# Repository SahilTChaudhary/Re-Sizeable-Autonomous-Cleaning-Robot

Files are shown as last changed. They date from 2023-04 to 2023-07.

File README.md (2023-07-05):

# ABSTRACT

Cleaning robots have advanced significantly in recent years, owing to their increased market presence and the desire for improved performance in cleaning. However, owing to their geometric restrictions with respect to the cleaning area, most robots have difficulty in cleaning the entire area. The robot developed in this paper uses on-board sensors, including ultrasonic sensors and camera to detect obstacles, change the robot configuration accordingly, and navigate forward, backward and even sideways with the help of Mecanum wheels. A ball screw linear actuator has been used to change the length of the robot according to what it maps about the room using the sensors. To achieve this, a precise CAD model has been developed according to the decided parameters. A functional prototype has also been developed as a proof of concept and it has been compared with a simulation study done in CoppeliaSim software.

---

**Work Done**

* Designed a CAD model using Fusion 360
* Calculated the Wheel Motor Torque requirements and the Battery Life
* Conducted a Simulation study in CoppeliaSim (V-REP)
* Programmed the Robot and Sensors using Raspberry Pi 4
* Conducted a Static Stress Analysis on the chassis of the robot using Ansys
* Built a Functional Prototype

<div style="text-align:center">
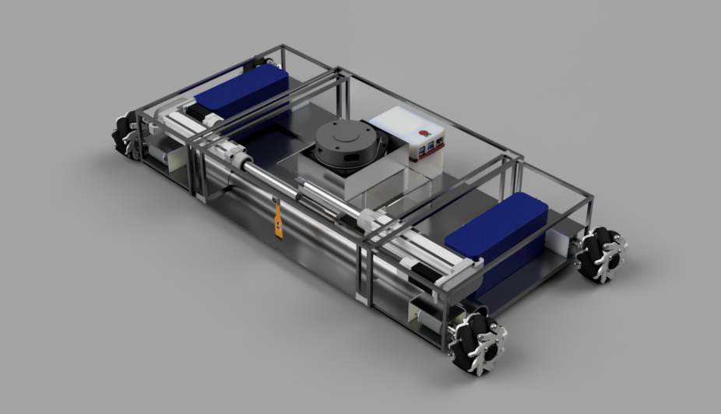
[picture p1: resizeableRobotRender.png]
cleaning_robot

</div>
<div style="text-align:center">
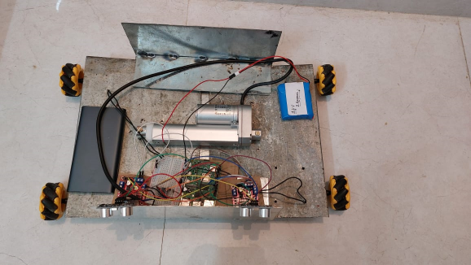
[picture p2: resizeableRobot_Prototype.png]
cleaning_robot

</div>

---

# CONCLUSION

A simulation study has been demonstrated to verify the efficacy of the system. Further, a functional prototype has been developed as a proof of concept to test the system in the real world. A static stress analysis has been conducted to determine the factor of safety of the chassis, which is the main load bearing element of the robot. Since the chassis is made of MS sheet, the weight of components will introduce stresses and bending. The stress analysis as well as the model developed prove that bending and subsequent failure are not a problem. Future work will involve integrating SLAM using LIDAR, for more efficient and systematic cleaning.
The analysis results show that the Factor of Safety is 15, hence the chassis will not fail. The maximum displacement is 0.3745 mm, which is at the middle box chassis. Further, the maximum stress induced is 14.75 MPa.
A Simulation environment has extremely ideal conditions, and there are no stresses induced on the robot. However, in the real world, there are several factors such as weight of components and friction that affect the performance of the robot. As a result, several iterations were required to attain a chassis that was performing well. Earlier iterations of the functional prototype suffered from bending of the chassis and loss of traction to the wheels. Having identified the problem areas, necessary modifications were made to the chassis to ensure compliance. After several iterations, a chassis was finally developed that functioned well. Such complications are not faced in a Simulation study, hence developing a functional prototype is of utmost importance, and has its own set of challenges.

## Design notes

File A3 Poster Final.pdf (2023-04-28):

References

Re-Sizeable Autonomous Cleaning Robot

Conclusion and Discussion

Introduction | Result and Discussion
- There is a strong demand for the application of cleaning robots in domestic settings. • Most robots in the market are of a fixed configuration. • Development of a re-sizeable robot that can increase its size in open spaces to cover more area in a single sweep, or can reduce its size to reach inaccessible areas is the focus of this project.

Scope of the Project

Presenter Details

- The project focuses on the development of a re-sizeable cleaning robot. The re-sizing mechanism can also be exported to other robots depending on needs.
- Definition of the problem statement and development of the Functional Architecture.
- Finalization of components and development of CAD model.
- Conduction of a Simulation study and development of a Functional Prototype as a proof of concept.

Methodology

- A simulation study has been conducted to demonstrate the efficacy of the system.
- A Functional Prototype has been developed to compare with the Simulation study.
- A stress analysis on the MS sheet used to make the chassis has been conducted. The FOS is 15.

A simulation study has been demonstrated to verify the efficacy of the system. Further, a functional prototype has been developed as a proof of concept to test the system in the real world. A static stress analysis has been conducted to
determine the factor of safety of the chassis, which is the main load bearing element of the robot. Since the chassis is made of MS sheet, the weight of components will introduce stresses and bending. The stress analysis as well as the model developed prove that bending and subsequent failure are not a problem. Future work will involve integrating SLAM using LIDAR, for more efficient and systematic cleaning.

Minimum Length

Maximum Length

- Designing and Optimization of An Autonomous Vacuum Floor Cleaning Robot
- Autonomous Self-Reconfigurable Floor Cleaning Robot
- Development of a Vacuum Cleaner Robot

SAHIL T CHAUDHARY – 18BME0668 KAHAAN PATEL – 18BME0691
MEHUL CHAURASIA – 18BME0640

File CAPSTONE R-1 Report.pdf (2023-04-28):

# Re-Sizeable Autonomous Cleaning Robot

### Submitted in partial fulfilment of the requirements for the degree of

# Bachelor of Technology

in

# Mechanical Engineering

By

### Sahil Chaudhary (18BME0668)

### Kahaan Patel (18BME0691)

### Mehul Chaurasia (18BME0640)

### Under the guidance of

### Prof. / Dr. Chinmaya Sahu

### Department of Design and Automation

School of Mechanical Engineering, VIT, Vellore.

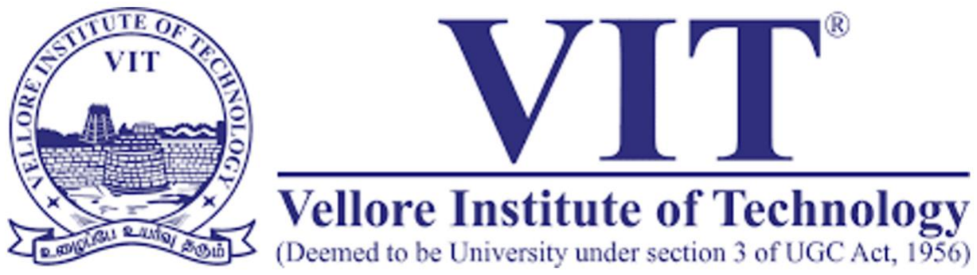
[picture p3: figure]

### February 2022

# Declaration

### We hereby declare that the thesis entitled “Re-Sizeable Autonomous Cleaning

### Robot" submitted by Kahaan Patel (18BME0691), Sahil Chaudhary

### (18BME0668) and Mehul Chaurasia (18BME0640), for the award of the degree

### of Bachelor of Technology in Mechanical Engineering to VIT is a record of

bonafide work carried out by me under the supervision of Dr. Chinmaya Sahu.

### We further declare that the work reported in this thesis has not been submitted

### and will not be submitted, either in part or in full, for the award of any other

degree or diploma in this institute or any other institute or university.

### Place: Vellore

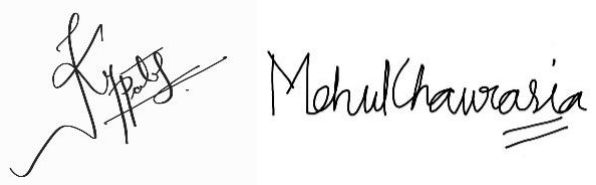
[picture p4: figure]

Date: 12th February 2022 | Signature of the Candidates

# Certificate

### This is to certify that the thesis entitled “Re-Sizeable Autonomous Cleaning

### Robot” submitted by Kahaan Patel (18BME0691), Sahil Chaudhary

### (18BME0668) and Mehul Chaurasia (18BME0640), School of Mechanical

### Engineering, VIT University, for the award of the degree of Bachelor of

### Technology in Mechanical Engineering, is a record of bonafide work carried out

### by them under my supervision during the period, 15.01.2022 to 20.04.2022, as

per the VIT code of academic and research ethics.

### The contents of this report have not been submitted and will not be submitted

### either in part or in full, for the award of any other degree or diploma in this

### institute or any other institute or university. The thesis fulfils the requirements

### and regulations of the University and in my opinion meets the necessary standards

for submission.

### Place: Vellore

Date: 12th February 2022 | Signature of the Guide
Internal Examiner | External Examiner

### Head of the Department

### School of Mechanical Engineering

# List of Contents

Contents | Page No.
Declaration | i
Certificate | ii
List of Contents | iii
Acknowledgement | iv
Abstract | 1
Introduction | 1
Literature Review | 2
Gaps in the Literature | 5
Problem Definition | 5
Objectives | 5
Methodology | 5
Worked Carried Out So Far | 5
Design Prototype | 6
Work to be Done | 8
Gantt Chart | 8
Milestones in the Project Phase | 8
References | 9

# Acknowledgement

We, Kahaan Patel, Sahil Chaudhary and Mehul Chaurasia would like to thank Dr. Chinmaya Sahu for his valuable guidance throughout the course of this project.

### We would also like to give a special thanks to Mukul Ganwal for his support

throughout the project.

### Abstract:

Cleaning robots have advanced significantly in recent years, owing to increased market presence and the demand for improved cleaning performance. However, due to geometric restrictions of the platforms in relation to the cleaning stage, as well as furniture and architecture, most robots have difficulty covering the whole cleaning area. The aim is to use the on-board sensors which will mainly be a combination of SLAM (Simultaneous Localization and Mapping) integrated using LIDAR and camera to detect obstacles and change the robot configuration accordingly and to navigate forward and backward and even sideways with the help of Mecanum wheels. The plan is to use a ball screw actuation mechanism to change the length of the robot according to what it maps about the local terrain using the sensors. For this purpose, a precise CAD model will be designed with the decided parameters so as to bring down the cost of making the cleaning robot to the bare minimum while also optimizing its cleaning efficiency at the same time.

### Introduction:

Cleaning has always been an important and necessary aspect of human lives, and it has developed and changed over time. The need for completely automated floor cleaning robots has surged as a result of today's hectic lifestyle.

Automated floor cleaning robots are commonly employed in smart homes, residential, and office spaces to clean the floors.

According to a world market study, there is a strong demand for the application of these robots in domestic settings with fully automated functionalities and the least amount of human assistance, and while these robots still account for a small percentage of the global vacuum cleaner market, their recognition and implementation is growing at a rapid rate.

The robots are small and execute the cleaning operation without the need for human participation. These robots use motion planning algorithms to cover a large area while cleaning, such as spiral motion, backtracking spiral motion, boustrophedon motion (back and forth), and basic zig-zag motion patterns.

Even though fixed-configuration robots have sufficient path planning and motion skills, they may require more time and energy to complete the complicated task effectively than their changeable counterparts. As a result, building a re-sizeable robot that can increase the swept area in open spaces, and can reduce its size to reach inaccessible areas. This project focuses on the design and development of the same.

### Literature Review:

Prassler et al. demonstrated almost how all commercial home cleaning robots are equipped with vacuum cleaners as their primary means of cleaning. Pool cleaning robots have also been developed. Some robots also have wet scrubbers to clean the floor (non-textile floor coverings), and some also clean carpets. Some industrial robots have sweepers along with vacuum cleaners. Duct cleaning robots with rotating brushes have also been developed. Sensors that are usually employed include Ultrasonic, LIDAR, IR, Cameras and Contact. Robots are navigated using dead-reckoning, manually using a joystick, or even using magnetic markers to guide the way. Safety features include front bumpers that absorb impact shock. Robot road sweepers have also been developed for cleaning large open spaces. [1]

Endres et al. developed robots for cleaning purposes in the supermarkets. There are some special features in these robots, they consist of a retractable wing which is inserted in the right part of the robot. The use of this retractable wing allows the robot to get close to the objects and precisely cleans the floor without colliding with the obstacles. Also, the size of this wing can be adjusted according to the requirement it can be extended or reduced as needed. The main features of this robot were: To identify the obstacles properly for cleaning the environment, executing the plan properly, no need to install any additional part to localize the robot, a systematic skill to move around the obstacles for least energy consumption. [2]

Kushal et al. have worked on a cleaning robot ATMEGA 2560 which worked with two modes: automatic and manual. The hardware used were Arduino Mega 2560, Ultrasonic Sensor, DC Generated Motor, Vacuum Motor, L298n Dual H-Bridge Motor Driver, VL53LOX Laser TOF Sensor and Servo Motor. Since the robot has two modes, one of them is manual mode which is selected when the robot switch is high and allows the users to reach places which are not automatically detected by the robot. And for the autonomous mode there is an algorithm which is followed by the robot with path planning. There is also a water sprayer attached so that the robot can also be used for the moping purposes as for the convenience of the user. [3]

Sewan Kim et al. demonstrated the Roboking system integration in an autonomous cleaning robot. The purpose of this robot was the protection of the indoor cleaning environment while the robot is working. There are many different sensors and the functions which are integrated in this system. The robot uses a digital signal processor from Texas Instruments (320LF 2406A). It works on 40MHz frequency with 24 sensors performing the operations together gathering different signals from internal subsystems. Also, there are 14 ultrasonic sensors which are installed in the robot, where nine of them were used in the lower part to find the obstacles. And the others were used on the upper part so that the robot does not collide with the tall obstacles. For the Roboking mechanism, there are cliff detecting sensors which determine the upliftment of the robot and prevent the robot from falling down. [4]

Liu et al. developed a system that did not rely on mapping and global self-localization. It consists of three layers. The lowest layer contains the sensors and hardware, which include ultrasonic (13 pairs, 7 for the front and the rest for the sides), IR, encoders, DC motors, vacuum etc. The second layer is responsible for the behaviour of the robot, which include point turning, line following, wall following, side shifting, and obstacle rounding. The third layer is responsible for carrying out tasks, like environment learning, cleaning and homing. [5]

Mahmud Hasan et al. demonstrated the use of bumper contact sensors and cliff IR sensors. The path planning algorithms include Random walk, spiral, ‘S’-shaped path and wall follow. These four algorithms are cycled between until the entire area is covered. The motor specification is 2Amp/6VDC, 5500 rpm with 70:1 gearbox for the driving wheels. The side brush controlling motor specification is 0.5Amp/6VDC with a 30:1 gearbox. The vacuum motor is 5Amp/6VDC with 8000rpm (Cyclonic type dry vacuum is used). The battery used is 6V/4.5Ah lead-acid. The robot can operate for an hour. The battery takes 5-6 hours to charge. [6]

Joon et al. developed a combination of Lidar and camera. A manipulator arm containing the vacuum was attached to the mobile robot. The collector box has a volume of 378 cubic cm (10 cm × 6 cm × 6.3 cm). [7]

Shakhawat Hossen et al. discussed how LIDAR and GPS have been used for mapping and localization. IR proximity sensors and ultrasonic sensors were used for object detection. [8]

Gerstmayr-Hillen et al. discussed how an omnidirectional camera was used to generate panoramic images of the environment in order to map it, and hence guide and navigate the robot to cover a rectangular segment of the robot’s workspace. The omnidirectional camera is used to simultaneously localize the robot and also map the environment. Hence, the camera carries out local visual homing and provides the data to generate a dense topological map. The robot is guided along parallel paths by controlling its distance from the previous lane. The distance is estimated using images from the camera and the robot’s odometry. Only the robot’s distance from the previous lane and its orientation are calculated. [9]

Karur et al. discussed various path planning algorithms. Dijkstra and A* algorithms are used for static environments, whereas D*RRT (Rapidly-Exploring Random Trees), Genetic, Ant Colony and Firefly algorithms are used for Dynamic environments. [10]

Dakulovic et al. demonstrated complete coverage of D* algorithm for path planning, using a combination of D* and PT algorithms. [11]

Lamini et al. demonstrated how GA (Genetic Algorithm) with improved crossover operators and fitness functions were employed to find optimal solutions. [12]

Amine Yakoubi et al. demonstrated that GA was used for path planning. Each gene represents the robot position and the chromosomes represent the mini-path. [13]

Liu et al. developed an algorithm for complete coverage path planning, which combines random path planning and local complete coverage path planning. Random path planning is very flexible for unstructured environments, but is inefficient. On the other hand, local complete coverage path planning generates a comb-like path to cover a relatively small area with high efficiency, but fails to do so in a larger area in an unstructured and dynamic environment. The proposed technique combined the benefits of both. 11 pairs of ultrasonic sensors were used, 7 for the front and the rest for the sides. [14]

Hofner et al. demonstrated path planning of a rectangular non-holonomic robot. Two changing maneuvers were used to navigate the robot – U-Turn and Side-Shift. Based on the parameters of the robot and the environment, the path planning algorithm will choose the most appropriate path planning template such that the entire floor area is covered efficiently. Localization was done using ultrasonic sensors and dead-reckoning. Subgoals were determined in the vicinity of various pre-planned landmarks. Vehicle guidance was done by finding the specified start location and compensation of path errors. [15]

Ramalingam et al. developed an algorithm for detecting and classifying debris as solid and liquid spillage using CNN and SVM was developed. This helped the robot to avoid hard to clean debris, as robots are mostly unable to clean such debris and hence end up spreading them on the floor rather than cleaning it, thus also reducing their efficiency. [16]

Schmidt et al. developed an algorithm that has been developed to memorize uncleaned areas that couldn’t be cleaned in the first sweep because of a temporary obstacle, and then come back to clean it after the remaining area has been cleaned. [17]

Parween et al. developed a self-reconfigurable robot called hTrihex has. It enables the robot to cover spaces that are generally missed or inaccessible by the usual circular shaped cleaning robots (like corners). This robot can configure itself into three different configurations based on the requirements, namely – Straight, Chevron and Closed. The sensors used onboard are encoders, LIDAR and IMU, along with a PID controller for implementing a closed-loop system. A differential drive has been implemented to steer the robot and hence control the heading. [18]

Parween et al. developed another similar self-reconfigurable robot is the hTetrakis. It consists of four equilateral triangles, and can change between three configurations namely – “I”, “A”, and “U” shapes. These configurations enable the robot to access convex and narrow corners that are generally inaccessible by the common circular shaped cleaning robots. [19]

Forlizzi et al. demonstrated that mecanum wheels have their omnidirectional property that allow them to have excellent manoeuvrability and ability to move in a congested space. Congested spaces usually mean environments with static or dynamic obstacles or narrow areas respectively. Due to the Mecanum wheel’s high manoeuvrability, it is ideal for outdoor applications like transportation purposes in warehouses, mining activities and even for military activities and indoor applications like autonomous robot cleaning that is the objective of this Capstone project. [20]

Laurena et al. developed and demonstrated control mechanism for actuating ball screw linear actuator. A ball screw linear actuator converts rotatory motion to linear motion. It has low friction and can withstand thrust loads. The programming and control system for the linear actuator was developed. [21]

Bhowmik et al. developed an algorithm for navigation of a cleaning robot by modifying the Dijkstra algorithm. A provision for backtracking and hill climbing were incorporated. This improved the performance of the Dijkstra algorithm. [22]

### Gaps in the Literature:

After the exhaustive literature review it has been concluded that,

1. All the commercially available cleaning robots are fixed in size and configuration.
2. A handful of self-reconfigurable robots have been developed. The aim of these robots is to cover hard-to-reach places, that conventional fixed configuration robots cannot.
3. Hence, the aim is to develop a re-sizeable robot that can increase its length to cover more area in a single sweep, and can also reduce its size to reach inaccessible areas.

### Problem Definition:

Cleaning robots are available in a variety of sizes and can clean a specific area in a single sweep. However, in open places with little impediment, such as broad halls and living rooms, cleaning can be done quickly by sweeping a larger area in a single sweep. To address this issue, a re- sizeable cleaning robot is being developed that can extend its length, allowing it to cover a larger area in a single sweep, and can also reduce its size to reach inaccessible areas.

### Objectives:

1. To design a system that can change the length of the robot depending on the need and area that is currently being cleaned.
2. To integrate an actuation mechanism for changing the length.
3. To integrate SLAM using LIDAR.
4. To integrate object detection using camera and/or ultrasonic sensors.

### Methodology:

The theoretical design of the robot, as well as the basic components needed, have been finalised after extensive study and detecting gaps in the literature review, as well as recognising scope for improvement. The following steps will be to create a CAD model, programme the robot's many functions like the ability to change its length according to the environment, and do simulations like controlling the opening and closing of the vacuum suction hole and the ability of the robot to manoeuvre with the help of Mecanum wheels. The on-board sensors will include LIDAR and camera to detect obstacles and change the robot configuration accordingly.

### Work Carried Out So Far:

1. Literature review has been completed.
2. Problem statement defined.
3. The primary components required to make the robot have been finalised.
4. The conceptual design of the robot, including the mechanism to change its size, has been developed.

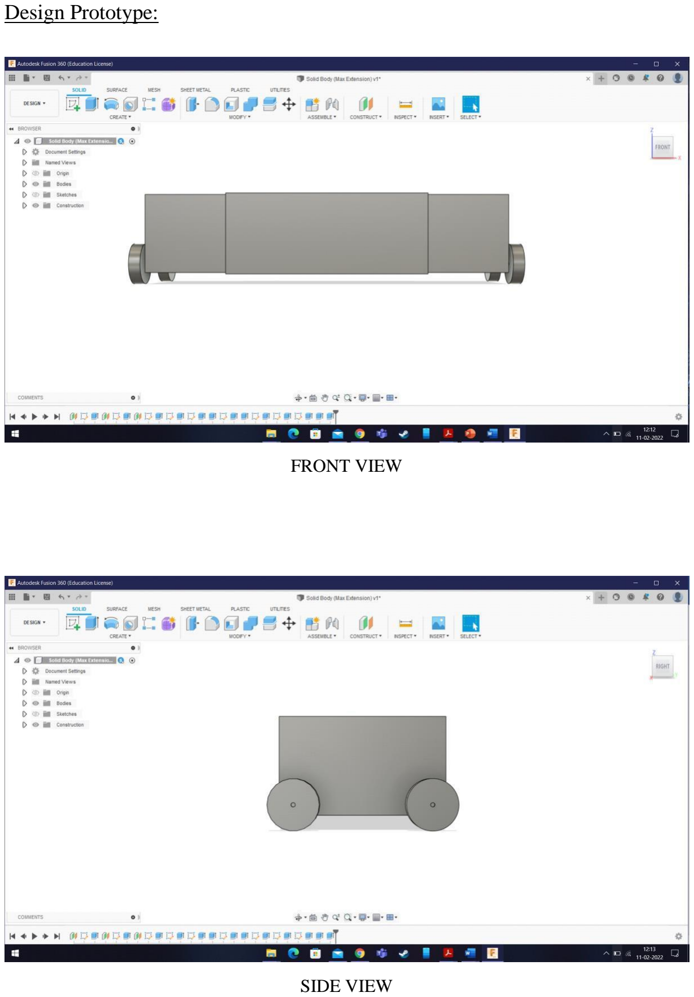
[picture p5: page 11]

### Design Prototype:

FRONT VIEW

SIDE VIEW

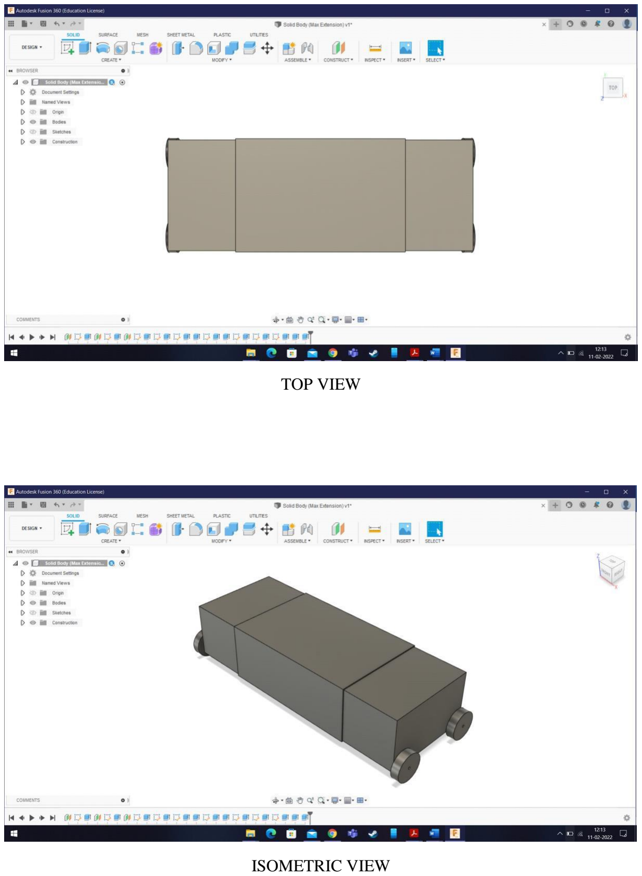
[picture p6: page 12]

TOP VIEW

ISOMETRIC VIEW

### Work to be Done:

1. A CAD model for the robot- After deciding upon the dimensions, the objective is to model it in Autodesk Fusion 360 so as to achieve the goal of making a re-sizeable autonomous robot that can change its dimensions according to the terrain.
2. Integrating SLAM using LIDAR and object detection using camera- Simultaneous Localization and Mapping will be used by the cleaning robot to create a map of the terrain and the concept of Light Detection and Ranging is used which collects information about variable distances between the robot and an obstruction using light in the form of a pulsed laser.
3. Developing the control system to actuate the Ball Screw Linear Actuator used to change the size (length) of the robot.
4. Integrating Mecanum wheels control in the robot.
5. Designing size changing vacuum slit for the robot- The size of the vacuum opening needs to change proportionally along with the length of the robot.
6. Integrating Dijkstra algorithm for path planning.

### Gantt Chart:

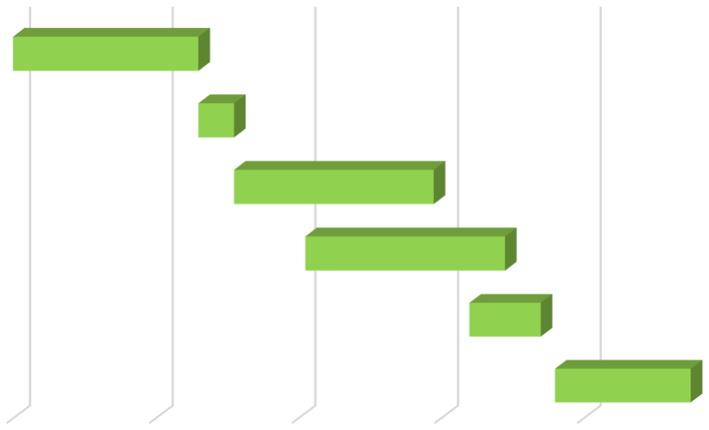
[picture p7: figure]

### Milestones in the Project Phase:

1. Chassis design
2. CAD design for actuation mechanism
15-Jan | 04-Feb | 24-Feb | 16-Mar | 05-Apr

Literature Review

Design Planning

Computer Aided Design

Coding

Integrating Everything

Simulation

| Everything Simulation | | Aided Design Coding Integrating Computer | Design Planning | Literature Review
Start Date | 01-Apr | 20-Mar | 25-Feb | 15-Feb | 10-Feb | 15-Jan
Days to Complete | 20 | 10 | 28 | 28 | 5 | 26

### Gantt Chart

3. Path Planning Algorithm
4. Object Detection Algorithm
5. Developing the control system to actuate the Ball Screw Linear Actuator used to change the size of the robot

### References:

[1] E. Prassler, A. Ritter, C. Schaeffer and P. Fiorini, “A Short History of Cleaning Robots,” Autonomous Robots, vol. 9, pp. 211-226, December 2000.
[2] H. Endres, W. Feiten and G. Lawitzky, “Field Test of a Navigation System: Autonomous Cleaning in Supermarkets,” IEEE International Conference on Robotics and Automation , 06 August 2002.
[3] N. Kushal, H. Chaudhuri and H. Nikithesh, “Autonomous Floor Cleaning Bot,” International Research Journal of Engineering and Technology (IRJET), vol. 5, no. 6, June 2018.
[4] S. Kim, “Autonomous Cleaning Robot: Roboking System Integration and Overview,” IEEE International Conference on Robotics and Automation, 07 June 2004.
[5] Y. Liu, S. Zhu, B. Jin, S. Feng and H. Gong, “Sensory Navigation of Autonomous Cleaning Robots,” Fifth World Congress on Intelligent Control and Automation, 18 October 2004.
[6] K. Hasan, A. Nahid and K. Reza, “Path Planning Algorithm Development for Autonomous Vacuum Cleaner Robots,” 2014 International Conference on Informatics, Electronics & Vision (ICIEV), May 2014.
[7] A. Joon and W. Kowalczyk, “Design of Autonomous Mobile Robot for Cleaning in the Environment with Obstacles,” Applied Science 2021, vol. 11, no. 17, p. 8076, 31 August 2021.
[8] S. Hossen, R. Shaharear, F. Islam, S. Islam, N. Hossain and S. Datta, “Designing and Optimization of An Autonomous Vacuum Floor Cleaning Robot,” in 2019 IEEE International Conference on Robotics, Automation, Artificial-intelligence and Internet-of-Things (RAAICON), November 2019.
[9] L. Gerstmayr-Hillen, F. Röben and M. Krzykawski, “Dense Topological Maps and Partial Pose Estimation for Visual Control of An Autonomous Cleaning Robot,” Robotics and Autonomous Systems, vol. 61, no. 5, May 2013.
[10] K. Karur, N. Sharma, C. Dharmatti and J. Siegel, “A Survey of Path Planning Algorithms for Mobile Robots,” Electrified Intelligent Transportation Systems, vol. 3, no. 3, pp. 448-468, 04 August 2021.

[11] M. Dakulović, S. Horvatić and I. Petrović, “Complete Coverage D* Algorithm for Path Planning of a Floor-Cleaning Mobile Robot,” IFAC Proceedings Volumes, vol. 44, no. 1, pp. 5950-5955, January 2011.
[12] C. Lamini, S. Benhlima and A. Elbekri, “Genetic Algorithm Based Approach for Autonomous Mobile Robot Path Planning,” Procedia Computer Science, vol. 127, pp. 180-189, 2018.
[13] M. Yakoubi and M. Laskri, “The Path Planning of Cleaner Robot for Coverage Region Using Genetic Algorithms,” Journal of Innovation in Digital Ecosystems, vol. 3, no. 1, pp. 37-43, June 2016.
[14] Y. Liu, X. Lin and S. Zhu, “Combined Coverage Path Planning for Autonomous Cleaning Robots in Unstructured Environments,” 2008 7th World Congress on Intelligent Control and Automation, 08 August 2008.
[15] C. Hofner and G. Schmidt, “Path Planning and Guidance Techniques for An Autonomous Mobile Cleaning Robot,” Robotics and Autonomous Systems, vol. 14, no. 2-3, pp. 199-212, May 1995.
[16] B. Ramalingam, A. Lakshmanan, M. Ilyas, A. Le and M. Elara, “Cascaded Machine-Learning Technique for Debris Classification in Floor-Cleaning Robot Application,” Applied Science 2018, vol. 8, no. 12, p. 2649, 17 December 2018.
[17] G. Schmidt and C. Hofner, “An Advanced Planning and Navigation Approach for Autonomous Cleaning Robot Operations,” International Conference on Intelligent Robots and Systems, 06 August 2002.
[18] R. Parween, M. Heredia, M. Rayguru and R. Abdulkader, “Autonomous Self-Reconfigurable Floor Cleaning Robot,” IEEE, pp. 114433-114442, 01 June 2020.
[19] R. Parween, V. Prabakaran, M. Elara and A. Vengadesh, “Application of Tiling Theory for Path Planning Strategy in a Polyiamond Inspired Reconfigurable Robot,” IEEE, pp. 6947-6957, 18 December 2018.
[20] J. Forlizzi and C. DiSalvo, “Service Robots in The Domestic Environment: A Study of The Roomba Vacuum in The Home,” HRI 06': Proceedings of the 1st ACM SIGCHI/SIGART Conference on Human-Robot Interaction, pp. 258-265, 02 March 2006.
[21] P. Eng, B. Laurean and D. Telea, “Management and Motion Control of Ball Screw Actuators Applied in the Robotic Structures,” Control Systems Engineering, June 2012.
[22] S. Bhowmick, R. Adhikari and S. Dutta, “Practical Applications for Mobile Robots based on Mecanum Wheels - A Systematic Survey,” IJIREEICE, vol. 6, no. 12, pp. 20-24, December 2018.
[23] M. Zhao, H. Lu, S. Yang, Y. Guo and F. Guo, “A Fast Robot Path Planning Algorithm Based on Bidirectional Associative Learning,” Computers & Industrial Engineering, vol. 155, p. 107173.

[24] A. Lakshmanan, R. Mohan, B. Ramalingam, A. Le, P. Veerajagadeshwar, K. Tiwari and
M. Ilyas, “Complete Coverage Path Planning Using Reinforcement Learning for Tetromino Based Cleaning and Maintenance Robot,” Automation in Construction, vol. 122, p. 103078, April 2020.
[25] Z. Yan, S. Schreiberhuber, G. Halmetschlager, T. Duckett, M. Vincze and N. Bellotto, “Robot Perception of Static and Dynamic Objects with An Autonomous Floor Scrubber,” Intelligent Service Robotics, pp. 403-417, 08 June 2020.
[26] H. Wang, Y. Yu and Q. Yuan, “Application Of Dijkstra Algorithm in Robot Path-Planning,” IEEE, 18 August 2011.
[27] L. Yang, J. Qi, D. Song, J. Xiao, J. Han and Y. Xia, “Survey of Robot 3D Path Planning Algorithms,” Journal of Control Science and Engineering, vol. 2016, no. Article ID 7426913, 04 July 2016.
[28] M. Elara, N. Rojas and A. Chua, “Design Principles for Robot Inclusive Spaces: A Case Study with Roomba,” IEEE, 29 September 2014.
[29] J. Jones, “Robots At the Tipping Point: The Road to iRobot Roomba,” IEEE, pp. 76-78, 2006 February 2006.
[30] Gross and Jennifer, “Interviewing Roomba: A Posthuman Study of Humans and Robot Vacuum Cleaners,” Explorations in Media Ecology, vol. 19, no. 3, pp. 285-297, 01 September 2020.
[31] B. Tribelhorn and Z. Dodds, “Evaluating The Roomba: A Low-Cost, Ubiquitous Platform for Robotics Research and Education,” IEEE, 21 May 2007.
[32] Bergman and Joel, “Robot Vaccum Cleaner,” School of Industrial Engineering and Management (ITM), p. 70, 2019.
[33] T. Asafa, T. Afonja, E. Olaniyan and H. Alade, “Development of a Vacuum Cleaner Robot,” Alexandria Engineering Journal, vol. 57, no. 4, pp. 2911-2920.
[34] Z. Zhang and Z. Zhao, “A Multiple Mobile Robots Path Planning Algorithm Based on A-Star and Dijkstra Algorithm,” International Journal of Smart Home, vol. 8, no. 3, pp. 75-86, May 2014.
[35] N. Buniyamin, W. Ngah, N. Sariff and Z. Mohamad, “A Simple Local Path Planning Algorithm for Autonomous Mobile Robots,” Control Systems Engineering, January 2011.
[36] M. Elara, N. Rojas and A. Chua, “Design Principles for Robot Inclusive Spaces: A Case Study with Roomba,” 2014 IEEE International Conference on Robotics and Automation (ICRA), 29 September 2014.

[37] P. Adithya, R. Tejas, S. Varun and B. Prashanth, “Design and Development of Automatic Cleaning and Mopping Robot,” IOP Conference Series: Materials Science and Engineering, vol. 577, no. 012126, 16 August 2018.
[38] M. Ilyas, S. Yuyao, R. Mohan, M. Devarassu and M. Kalimuthu, “Design of sTetro: A Modular, Reconfigurable, and Autonomous Staircase Cleaning Robot,” Journal of Sensors, vol. 2018, no. Article ID 8190802, 24 July 2018.
[39] T. Ichimura and S.-i. Nakajima, “Development of an autonomous beach cleaning robot “Hirottaro”,” 2016 IEEE International Conference on Mechatronics and Automation, 05 September 2016.
[40] V. N. Shah, Sathvik and A. Vaghela, “Floor Cleaning Robot (Autonomus/Manual),” International Journal of Engineering Research & Technology (IJERT), no. 2016.
[41] V. Silva, J. Roche and A. Kondoz, “Robust Fusion of LiDAR and Wide-Angle Camera Data for Autonomous Mobile Robots,” Sensors 2018, Depth Sensors and 3D Vision, vol. 18, no. 8, p. 2730, 20 August 2018.
[42] C. E. O. Lima and S. Sano, “Design and Analysis of a New Type of Mecanum Wheel,” in Proceedings of 175th IASTEM International Conference – Tokyo, Japan, April 2019.

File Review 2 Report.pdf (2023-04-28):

# Re-Sizeable Autonomous Cleaning Robot

### Submitted in partial fulfilment of the requirements for the degree of

# Bachelor of Technology

in

# Mechanical Engineering

By

### Sahil Chaudhary (18BME0668)

### Kahaan Patel (18BME0691)

### Mehul Chaurasia (18BME0640)

### Under the guidance of

### Prof. / Dr. Chinmaya Sahu

### Department of Design and Automation

School of Mechanical Engineering, VIT, Vellore.

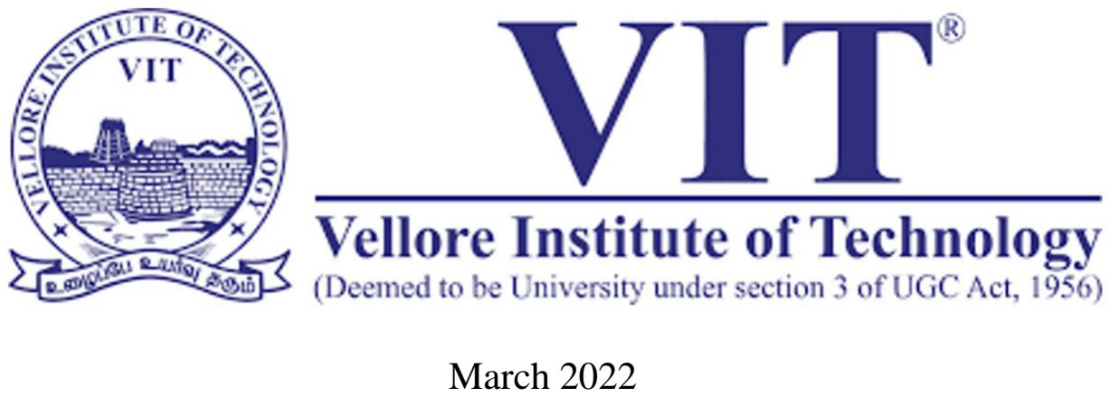
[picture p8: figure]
March 2022

# Declaration

### We hereby declare that the thesis entitled “Re-Sizeable Autonomous Cleaning

### Robot" submitted by Kahaan Patel (18BME0691), Sahil Chaudhary

### (18BME0668) and Mehul Chaurasia (18BME0640), for the award of the degree

### of Bachelor of Technology in Mechanical Engineering to VIT is a record of

bonafide work carried out by me under the supervision of Dr. Chinmaya Sahu.

### We further declare that the work reported in this thesis has not been submitted

### and will not be submitted, either in part or in full, for the award of any other

degree or diploma in this institute or any other institute or university.

### Place: Vellore


Date: 28th March 2022 | Signature of the Candidates

# Certificate

### This is to certify that the thesis entitled “Re-Sizeable Autonomous Cleaning

### Robot” submitted by Kahaan Patel (18BME0691), Sahil Chaudhary

### (18BME0668) and Mehul Chaurasia (18BME0640), School of Mechanical

### Engineering, VIT University, for the award of the degree of Bachelor of

### Technology in Mechanical Engineering, is a record of bonafide work carried out

### by them under my supervision during the period, 15.01.2022 to 20.04.2022, as

per the VIT code of academic and research ethics.

### The contents of this report have not been submitted and will not be submitted

### either in part or in full, for the award of any other degree or diploma in this

### institute or any other institute or university. The thesis fulfils the requirements

### and regulations of the University and in my opinion meets the necessary standards

for submission.

### Place: Vellore

Date: 28th March 2022 | Signature of the Guide
Internal Examiner | External Examiner

### Head of the Department

### School of Mechanical Engineering

# List of Contents

Contents | Page No.
Declaration | i
Certificate | ii
List of Contents | iii
Acknowledgement | iv
Abstract | 1
Introduction | 1
Literature Review | 2
Gaps in the Literature | 5
Problem Definition | 5
Objectives | 5
Methodology | 5
Work Carried Out | 7
Functional Architecture | 7
Circuit Diagram | 9
Design Calculations | 9
Component Table | 11
Component Images | 12
Design Prototype | 17
CAD Design | 19
Simulation | 27
Work to be Done | 27
Gantt Chart | 28
Milestones in the Project | 28
Summary | 28

References

2

9

References (Figures) | 32

# Acknowledgement

We, Kahaan Patel, Sahil Chaudhary and Mehul Chaurasia would like to thank Dr. Chinmaya Sahu for his valuable guidance throughout the course of this project.

### We would also like to give a special thanks to Mukul Ganwal for his support

throughout the project.

### Abstract:

Cleaning robots have advanced significantly in recent years, owing to increased market presence and the demand for improved cleaning performance. However, due to geometric restrictions of the platforms in relation to the cleaning stage, as well as furniture and architecture, most robots have difficulty covering the whole cleaning area. The aim is to use the on-board sensors which will mainly be a combination of SLAM (Simultaneous Localization and Mapping) integrated using LIDAR and camera to detect obstacles and change the robot configuration accordingly and to navigate forward and backward and even sideways with the help of mecanum wheels. The plan is to use a ball screw actuation mechanism to change the length of the robot according to what it maps about the local terrain using the sensors. For this purpose, a precise CAD model will be designed with the decided parameters so as to bring down the cost of making the cleaning robot to the bare minimum while also optimizing its cleaning efficiency at the same time.

### Introduction:

Cleaning has always been an important and necessary aspect of human lives, and it has developed and changed over time. The need for completely automated floor cleaning robots has surged as a result of today's hectic lifestyle.

Automated floor cleaning robots are commonly employed in smart homes, residential, and office spaces to clean the floors.

According to a world market study, there is a strong demand for the application of these robots in domestic settings with fully automated functionalities and the least amount of human assistance, and while these robots still account for a small percentage of the global vacuum cleaner market, their recognition and implementation is growing at a rapid rate.

The robots are small and execute the cleaning operation without the need for human participation. These robots use motion planning algorithms to cover a large area while cleaning, such as spiral motion, backtracking spiral motion, boustrophedon motion (back and forth), and basic zig-zag motion patterns.

Even though fixed-configuration robots have sufficient path planning and motion skills, they may require more time and energy to complete the complicated task effectively than their changeable counterparts. As a result, building a re-sizeable robot that can increase the swept area in open spaces can reduce the time taken to clean. This project focuses on the design and development of the same.

### Literature Review:

Prassler et al. demonstrated almost how all commercial home cleaning robots are equipped with vacuum cleaners as their primary means of cleaning. Pool cleaning robots have also been developed. Some robots also have wet scrubbers to clean the floor (non-textile floor coverings), and some also clean carpets. Some industrial robots have sweepers along with vacuum cleaners. Duct cleaning robots with rotating brushes have also been developed. Sensors that are usually employed include Ultrasonic, LIDAR, IR, Cameras and Contact. Robots are navigated using dead-reckoning, manually using a joystick, or even using magnetic markers to guide the way. Safety features include front bumpers that absorb impact shock. Robot road sweepers have also been developed for cleaning large open spaces. [1]

Endres et al. developed robots for cleaning purposes in the supermarkets. There are some special features in these robots, they consist of a retractable wing which is inserted in the right part of the robot. The use of this retractable wing allows the robot to get close to the objects and precisely cleans the floor without colliding with the obstacles. Also, the size of this wing can be adjusted according to the requirement it can be extended or reduced as needed. The main features of this robot were: To identify the obstacles properly for cleaning the environment, executing the plan properly, no need to install any additional part to localize the robot, a systematic skill to move around the obstacles for least energy consumption. [2]

Kushal et al. have worked on a cleaning robot ATMEGA 2560 which worked with two modes: automatic and manual. The hardware used were Arduino Mega 2560, Ultrasonic Sensor, DC Generated Motor, Vacuum Motor, L298n Dual H-Bridge Motor Driver, VL53LOX Laser TOF Sensor and Servo Motor. Since the robot has two modes, one of them is manual mode which is selected when the robot switch is high and allows the users to reach places which are not automatically detected by the robot. And for the autonomous mode there is an algorithm which is followed by the robot with path planning. There is also a water sprayer attached so that the robot can also be used for the moping purposes as for the convenience of the user. [3]

Sewan Kim et al. demonstrated the Roboking system integration in an autonomous cleaning robot. The purpose of this robot was the protection of the indoor cleaning environment while the robot is working. There are many different sensors and the functions which are integrated in this system. The robot uses a digital signal processor from Texas Instruments (320LF 2406A). It works on 40MHz frequency with 24 sensors performing the operations together gathering different signals from internal subsystems. Also, there are 14 ultrasonic sensors which are installed in the robot, where nine of them were used in the lower part to find the obstacles. And the others were used on the upper part so that the robot does not collide with the tall obstacles. For the Roboking mechanism, there are cliff detecting sensors which determine the upliftment of the robot and prevent the robot from falling down. [4]

Liu et al. developed a system that did not rely on mapping and global self-localization. It consists of three layers. The lowest layer contains the sensors and hardware, which include ultrasonic (13 pairs, 7 for the front and the rest for the sides), IR, encoders, DC motors, vacuum etc. The second layer is responsible for the behaviour of the robot, which include point turning, line following, wall following, side shifting, and obstacle rounding. The third layer is responsible for carrying out tasks, like environment learning, cleaning and homing. [5]

Mahmud Hasan et al. demonstrated the use of bumper contact sensors and cliff IR sensors. The path planning algorithms include Random walk, spiral, ‘S’-shaped path and wall follow. These four algorithms are cycled between until the entire area is covered. The motor specification is 2Amp/6VDC, 5500 rpm with 70:1 gearbox for the driving wheels. The side brush controlling motor specification is 0.5Amp/6VDC with a 30:1 gearbox. The vacuum motor is 5Amp/6VDC with 8000rpm (Cyclonic type dry vacuum is used). The battery used is 6V/4.5Ah lead-acid. The robot can operate for an hour. The battery takes 5-6 hours to charge. [6]

Joon et al. developed a combination of Lidar and camera. A manipulator arm containing the vacuum was attached to the mobile robot. The collector box has a volume of 378 cubic cm (10 cm × 6 cm × 6.3 cm). [7]

Shakhawat Hossen et al. discussed how LIDAR and GPS have been used for mapping and localization. IR proximity sensors and ultrasonic sensors were used for object detection. [8]

Gerstmayr-Hillen et al. discussed how an omnidirectional camera was used to generate panoramic images of the environment in order to map it, and hence guide and navigate the robot to cover a rectangular segment of the robot’s workspace. The omnidirectional camera is used to simultaneously localize the robot and also map the environment. Hence, the camera carries out local visual homing and provides the data to generate a dense topological map. The robot is guided along parallel paths by controlling its distance from the previous lane. The distance is estimated using images from the camera and the robot’s odometry. Only the robot’s distance from the previous lane and its orientation are calculated. [9]

Karur et al. discussed various path planning algorithms. Dijkstra and A* algorithms are used for static environments, whereas D*RRT (Rapidly-Exploring Random Trees), Genetic, Ant Colony and Firefly algorithms are used for Dynamic environments. [10]

Dakulovic et al. demonstrated complete coverage of D* algorithm for path planning, using a combination of D* and PT algorithms. [11]

Lamini et al. demonstrated how GA (Genetic Algorithm) with improved crossover operators and fitness functions were employed to find optimal solutions. [12]

Amine Yakoubi et al. demonstrated that GA was used for path planning. Each gene represents the robot position and the chromosomes represent the mini-path. [13]

Liu et al. developed an algorithm for complete coverage path planning, which combines random path planning and local complete coverage path planning. Random path planning is very flexible for unstructured environments, but is inefficient. On the other hand, local complete coverage path planning generates a comb-like path to cover a relatively small area with high efficiency, but fails to do so in a larger area in an unstructured and dynamic environment. The proposed technique combined the benefits of both. 11 pairs of ultrasonic sensors were used, 7 for the front and the rest for the sides. [14]

Hofner et al. demonstrated path planning of a rectangular non-holonomic robot. Two changing maneuvers were used to navigate the robot – U-Turn and Side-Shift. Based on the parameters of the robot and the environment, the path planning algorithm will choose the most appropriate path planning template such that the entire floor area is covered efficiently. Localization was done using ultrasonic sensors and dead-reckoning. Subgoals were determined in the vicinity of various pre-planned landmarks. Vehicle guidance was done by finding the specified start location and compensation of path errors. [15]

Ramalingam et al. developed an algorithm for detecting and classifying debris as solid and liquid spillage using CNN and SVM was developed. This helped the robot to avoid hard to clean debris, as robots are mostly unable to clean such debris and hence end up spreading them on the floor rather than cleaning it, thus also reducing their efficiency. [16]

Schmidt et al. developed an algorithm that has been developed to memorize uncleaned areas that couldn’t be cleaned in the first sweep because of a temporary obstacle, and then come back to clean it after the remaining area has been cleaned. [17]

Parween et al. developed a self-reconfigurable robot called hTrihex has. It enables the robot to cover spaces that are generally missed or inaccessible by the usual circular shaped cleaning robots (like corners). This robot can configure itself into three different configurations based on the requirements, namely – Straight, Chevron and Closed. The sensors used onboard are encoders, LIDAR and IMU, along with a PID controller for implementing a closed-loop system. A differential drive has been implemented to steer the robot and hence control the heading. [18]

Parween et al. developed another similar self-reconfigurable robot is the hTetrakis. It consists of four equilateral triangles, and can change between three configurations namely – “I”, “A”, and “U” shapes. These configurations enable the robot to access convex and narrow corners that are generally inaccessible by the common circular shaped cleaning robots. [19]

Forlizzi et al. demonstrated that mecanum wheels have their omnidirectional property that allow them to have excellent manoeuvrability and ability to move in a congested space. Congested spaces usually mean environments with static or dynamic obstacles or narrow areas respectively. Due to the Mecanum wheel’s high manoeuvrability, it is ideal for outdoor applications like transportation purposes in warehouses, mining activities and even for military activities and indoor applications like autonomous robot cleaning that is the objective of this Capstone project. [20]

Laurena et al. developed and demonstrated control mechanism for actuating ball screw linear actuator. A ball screw linear actuator converts rotatory motion to linear motion. It has low friction and can withstand thrust loads. The programming and control system for the linear actuator was developed. [21]

Bhowmik et al. developed an algorithm for navigation of a cleaning robot by modifying the Dijkstra algorithm. A provision for backtracking and hill climbing were incorporated. This improved the performance of the Dijkstra algorithm. [22]

### Gaps in the Literature:

After the exhaustive literature review it has been concluded that,

1. According to the literature review conducted, all the cleaning robots including the commercially available ones, are fixed in size and configuration.
2. A handful of self-reconfigurable robots have been developed. The objective of these robots is to cover hard-to-reach places, that conventional fixed configuration robots cannot.
3. Hence, the aim is to develop a re-sizeable robot that can increase its length to cover more area in a single sweep, and can also reduce its size to reach inaccessible areas.

### Problem Definition:

Cleaning robots are available in a variety of sizes and can clean a specific area in a single sweep. However, the cleaning efficiency and effectiveness can be improved. In open places with little impediment, such as broad halls and living rooms, cleaning can be done quickly by sweeping a larger area in a single sweep. To address this problem, a re-sizeable cleaning robot is being developed that can extend its length, allowing it to cover a larger area in a single sweep, and can also reduce its size to reach inaccessible areas.

### Objectives:

1. To design a system that can change the length of the robot depending on the need and area that is currently being cleaned.
2. To integrate an actuation mechanism for changing the length.
3. To integrate SLAM using LIDAR.
4. To integrate object detection using camera and/or ultrasonic sensors.
5. To conduct a Simulation study.

### Methodology:

The theoretical design of the robot, as well as the basic components needed, have been finalised after extensive study and detecting gaps in the literature review, as well as recognising scope for improvement. The CAD model has been developed, based on the mathematical calculations and finalised components. The on-board sensors include LIDAR and camera to detect obstacles and change the robot configuration accordingly. The following steps include programming the robot's many functions like the ability to change its length according to the environment, and conducting simulations like controlling the size of the robot and the ability of the robot to manoeuvre with the help of Mecanum wheels. The primary components that have been used are:

1. LIDAR– LIDAR (Light Detection and Ranging) is a remote sensing technique that measures ranges (varying distances) to the obstacle using light in the form of a pulsed laser.

The aim is to use RPLIDAR A1 which integrates the concept of SLAM (Simultaneous Localization and Mapping). RPLIDAR A1 is a laser triangulation range system that employs Slamtec's high-speed vision acquisition and processing hardware. The technology takes distance measurements at a rate of around 8000 times per second. RPLIDAR A1's core rotates clockwise to perform 360-degree omnidirectional laser range scanning for its surrounding surroundings and then build an outline map.

2. Mecanum Wheels – Mecanum wheels have their omnidirectional property that allow them to have excellent manoeuvrability and ability to move in a congested space. Congested spaces usually mean environments with static or dynamic obstacles, or with narrow areas.

The aim is to use a set of bush type aluminium Mecanum wheels with the following specifications:

i) Diameter: 60 x 31 mm (Diameter x Width)
ii) Body Material: Aluminium Alloy
iii) Roller Material: Hard Rubber
iv) Length of Roller: 30 mm
v) Net Weight: 93 gm (Each)
vi) Load Capacity: 3Kg/Wheel
3. Camera – The aim is to use a camera sensor for object detection so as to facilitate the cleaning robot to make its own autonomous decision. The objective is to use the Raspberry PI 5MP Camera Board Module. It will also enable a live video feed to be transmitted to any device via Wi-Fi or Bluetooth.
4. Raspberry Pi – The aim is to use Raspberry Pi 4 microprocessor as it is easier to integrate it with the SLAM based RPLIDAR A1 so as to facilitate smoother mapping of the terrain. Raspberry Pi 4 will be used specifically due to its high-performance 64-bit quad-core processor, 4 GB of RAM and dual display support with resolutions up to 4K via a pair of micro-HDMI ports.
5. Battery Pack – The aim is to use two 5000mAh 22.2V battery packs with maximum discharge current and maximum charging current as 15000 mA and 5000 mA respectively. Instead of using one big 10000mAh battery, the plan is to use two 5000mAh battery connected in parallel as the voltage remains constant and increase the duration for which it could power equipment. It’s important to note that when charging batteries that are connected in parallel, the increased amp-hour capacity may require a longer charge time.
6. IMU – The aim is to use MPU9250 9-Axis Attitude Gyro Accelerator Magnetometer Sensor Module with a power supply of 3.3-5 V (DC) and dimensions 22 X 17 mm with 9 DOF modules.
7. Wheel Motor – The aim is to use a compact DC Motor with High Power Density and high efficiency. The following are its characteristics:

i) Input Voltage of 12 V (DC)
ii) No Load Speed = 9900 rpm
iii) Nominal Speed = 8050 rpm
iv) Maximum Output power = 6.64 W
v) Life (Typical) = 1000 hrs
8. Ball Screw Actuator – Ball screws are mechanical linear actuators made up of a screw shaft and a nut with a ball that rolls between helical grooves that correspond. Ball screws' main purpose is to transform rotational motion into linear motion. Ball nuts are used to transmit forces to a static or dynamic load with excellent precision, reproducibility, and accuracy. The rolling balls in the helical groove of ball screws are a unique feature that eliminates mechanical contact inside the screw assembly and replaces sliding friction with rolling friction. This technique reduces friction greatly, resulting in a very efficient power conversion. Screw efficiency is determined by their capacity to convert power used to exert rotating force into linear distance travelled.

The aim is to use ball screw linear actuators to control the size of the robot.

### Work Carried Out:

1. Literature review has been completed.
2. Problem statement defined.
3. The primary components required to make the robot have been finalised.
4. The conceptual design of the robot, including the mechanism to change its size, has been developed.
5. The Functional Architecture has been developed.
6. Mathematical analysis required for the research has been conducted.
7. The components have been finalized.
8. A detailed CAD Model has been developed.
9. Basic Simulation study has been initiated.

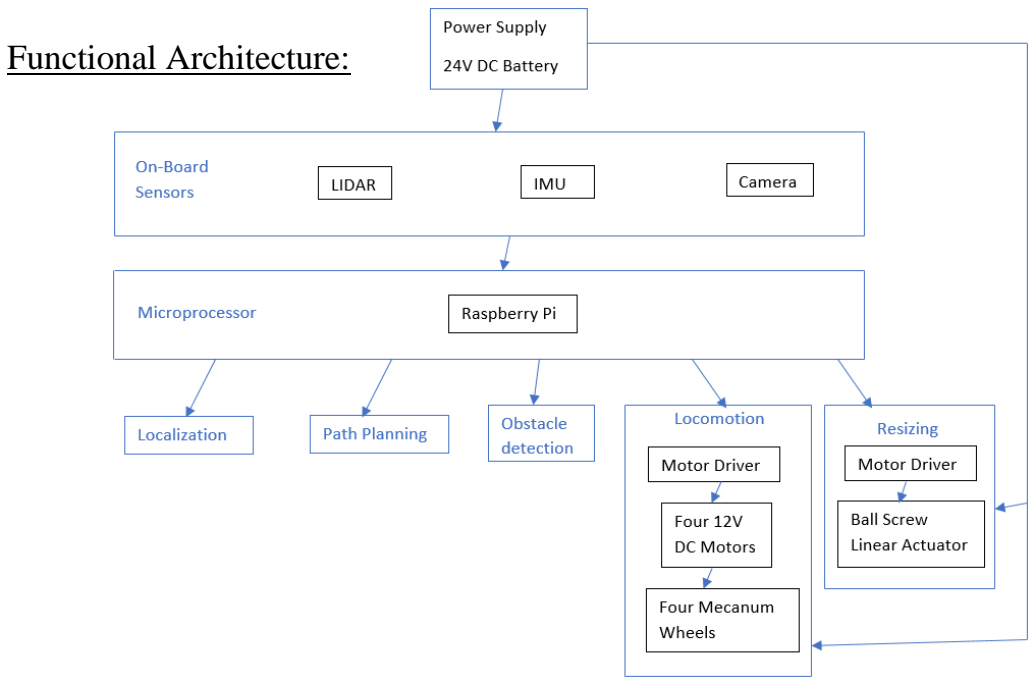
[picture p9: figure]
Functional Architecture:

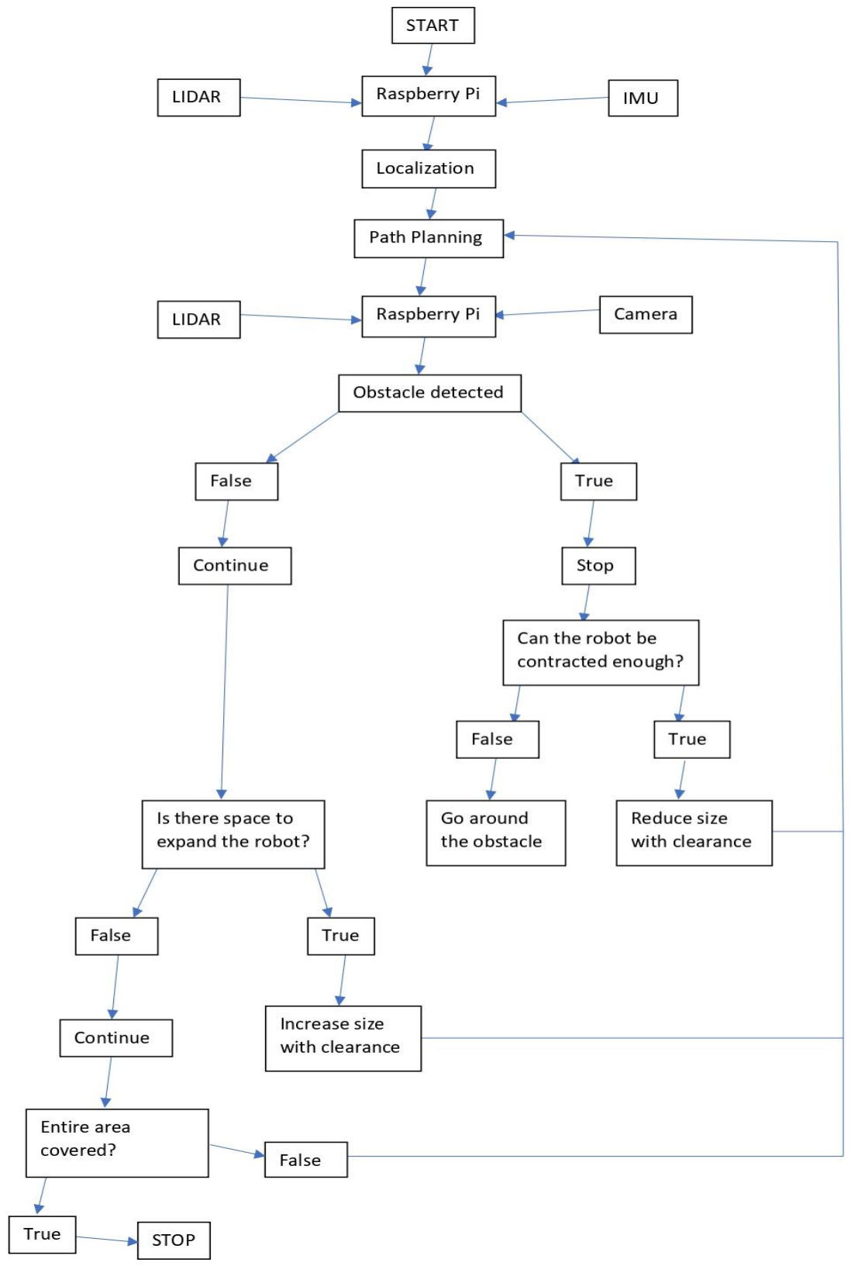
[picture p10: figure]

### Circuit Diagram:

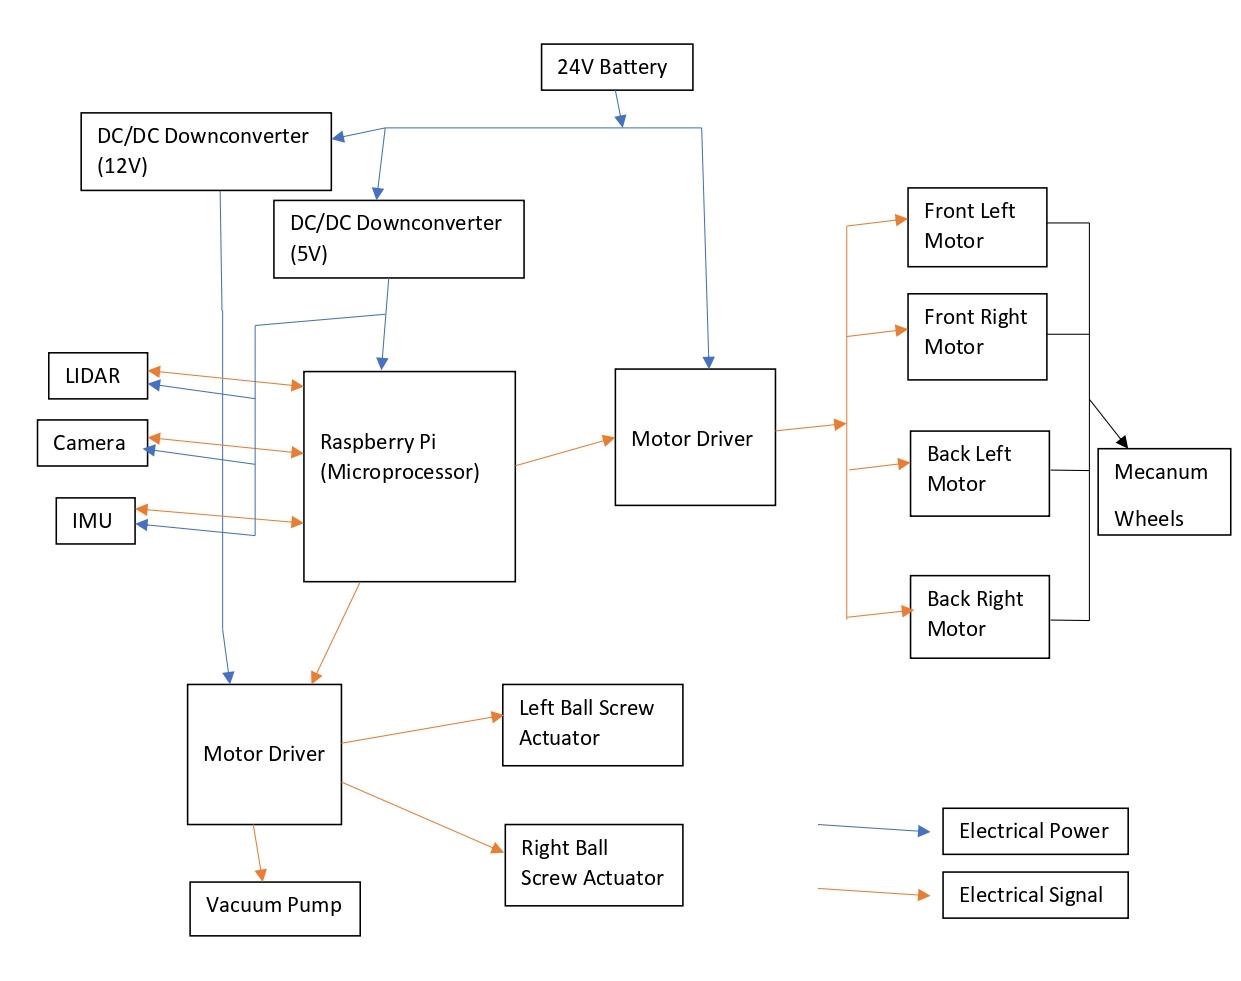
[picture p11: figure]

### Design Calculations:

Wheel Motor Torque Calculation for the 4 Mecanum Wheels:

Mass of Cleaning Robot = 9 kg
Radius of wheel = 0.03 m

τ = μ ∗ m ∗ g ∗ R

1. Case 1 (Wooden Floor)

Coefficient of Friction between hard rubber and wooden floor = 0.7 Total Torque = 9*9.81*0.7*0.03 = 1.85409 Nm
Individual Torque of each motor = 1.85409/4 = 0.4635225 Nm
2. Case 2 (Ceramic)

Coefficient of Friction between hard rubber and ceramic tile = 0.32 Total Torque = 9*9.81*0.32*0.03 = 0.847584 Nm

Individual Torque of each motor = 0.847584/4 = 0.211896 Nm

3. Case 3 (Marble)

Coefficient of Friction between hard rubber and marble tile = 0.25 Total Torque = 9*9.81*0.25*0.03 = 0.662175 Nm
Individual Torque of each motor = 0.662175/4 = 0.16554375 Nm
4. Case 4 (Smooth Concrete)

Coefficient of Friction between hard rubber and smooth concrete surface = 0.38 Total Torque = 9*9.81*0.38*0.03 = 1.006506 Nm
Individual Torque of each motor = 1.006506/4 = 0.2516265 Nm
5. Case 5 (Rough Concrete)

Coefficient of Friction between hard rubber and rough concrete surface = 0.62 Total Torque = 9*9.81*0.62*0.03 = 1.642194 Nm
Individual Torque of each motor = 1.642194/4 = 0.4105485 Nm

### Vacuum System Calculations:

Taking D = 3 cm (1.1811 in), and L = 5 cm (1.9685 in)

Speed of pump, Sp = 49.3 CFM = 23.267 L/s

Now,

Conductance of the system,

C =

78 ∗ D

3
L

C =

78 ∗ 1.1811³
1.9685 = 65.2858 L/s

∴ C = 133.3327 CFM

Therefore,

Effective pump speed, S
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
23.267 +
| 1
| 133.3327

∴ S = 19.81 CFM

Now,

Velocity at orifice,

When robot is fully extended: A = 50 x 0.5 cm² = 0.0269098 ft²

Q = Av

∴ v =

19.81
0.0269098 = 736.163 ft/min

v = 3.74 m/s

When robot is at minimum extension: A = 30 x 0.5 cm² = 0.01614 ft²

Q = Av

∴ v =

19.81
0.01614 = 1227.385 ft/min

v = 6.235 m/s

### Battery Life Calculations:

Essential Components:

1. Units of Motors = 15*4 = 60 W
2. Vacuum Pump = 40 W
3. RPLIDAR A1 = 0.5 W
4. Camera = 7.5 W
5. Raspberry Pi 4 Model B = 25 W

Total Power Consumption by the essential components = 133 W

Rounded off to 135 W for ease of battery life calculations.

Battery type chosen is Lithium-ion

Battery Life = 240 Watt-Hour/135 W = 1.78 hours = 106.8 mins = 107 mins (Rounded off)

### Component Table:

Component | Qty | Specs/Model Name | Dimensions | Weight | Price (Rs.)
LIDAR | 1 | RPLIDAR A1 | 98.5 x 70 x 60 mm | 170 g | 8,549

Mecanum Wheels | 4 | 45° in Tank Drive configuration, Load 3Kg/wheel | 60 x 31 mm (Diameter x Width) | 93 g (per wheel) | 5,549
Vacuum Pump | 1 | Nidec G10D | 97 x 94 x 33 mm | 180 g | 8,538
Dust box | 1 | With HEPA Filter | 600 ml | 87 g | 150
Battery pack | 2 | Orange 18650 Li-ion 5000mAh-6s-22.2v-3c 6S2P | 160 x 100 x 50 mm (for 1) | 770 g (x2) | 3,299 (x2)
Wheel Motor | 4 | Johnson Geared Motor (Grade B) 12 V DC | Ø 27 X 64 mm (for 1) | 164 g (x4) | 384 (x4)
Motor Driver | 2 | L298N 2A Based Motor Driver Module | 44 x 44 x 28 mm | 25 g (x2) | 129 (x2)
Raspberry Pi | 1 | Raspberry Pi 4 Model B 4GB | 85.6mm x 56.5mm | 52 g | 5,149
Camera | 1 | Raspberry PI 5MP Camera Board Module | 4 x 3 x 2 cm | 10 g | 389
IMU | | MPU9250 9-Axis Attitude Gyro Accelerator Magnetometer Sensor Module | 25 x 15 x 3.5 mm | 5 g | 749
Ball Screw Actuator | 2 | Linear Actuator Stroke Length 100MM,7mm/S,1500N,12V | 210 x 74 x 36 mm | 889 g (x2) | 3900 (x2)
DC/DC Converter | 1 | 24V/12V to 5V 5A Power Module DC-DC XY-3606 Power Converter | 63 x 27 x10 mm | 22 g | 289
DC/DC Converter | 1 | A2412S-1WR2 Mornsun 24V to ±12V DC-DC Converter 1W Power Supply Module - Ultra Compact SIP Package | 19.5 x 6 x 9.3 mm | 2.4 g | 395

### Component Images:

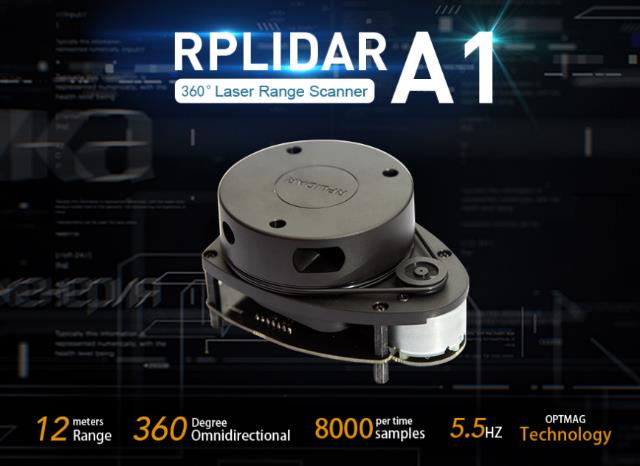
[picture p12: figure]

1. LIDAR Scanner:

[Figure 1]

RPLIDAR A1 has been chosen as it has been specifically designed for indoor robotic SLAM applications, and has been designed for the Raspberry Pi 4 Model B microprocessor, which is the microprocessor used in the robot.

2. Mecanum Wheel:
i) Φ60 mm
ii) Load Capacity: 3Kg/Wheel iii) Body Material: Al Alloy iv) Length of Roller: 30 mm

Mecanum wheels with 45° roller orientation have been chosen for the added manoeuvrability and degrees of freedom they provide, such as strafing and turning on the spot.

3. Vacuum Pump:
i) Model: Nidec G10D
ii) Rated speed: 5700 RPM
iii) Max. Airflow: 49.3 CFM iv) Max. Static Pressure: 395 Pa
v) Rated Voltage: 12 V
vi) Rated Input: 38.4 W

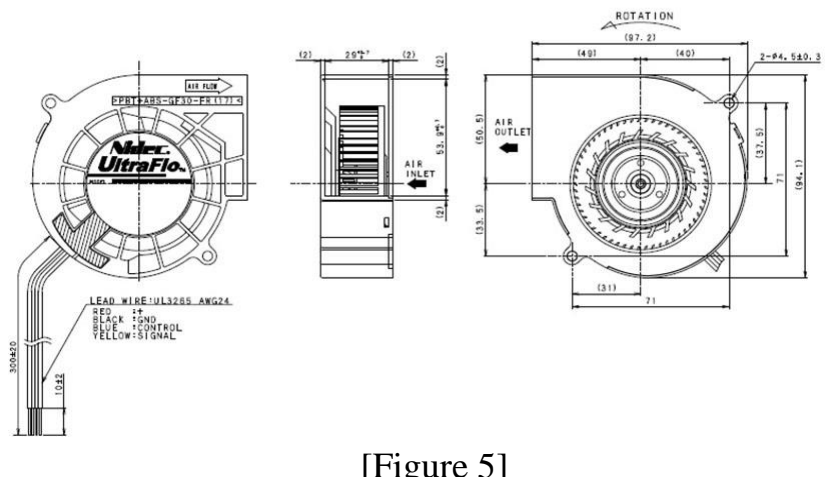
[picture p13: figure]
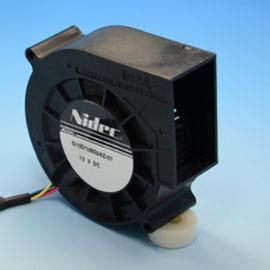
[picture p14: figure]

The vacuum pump has been chosen on the basis of space available inside the robot, and the maximum discharge that it can provide, measured in CFM (Cubic Feet per Minute).

[Figure 2]

[Figure 5]
[Figure 4]

[Figure 3]

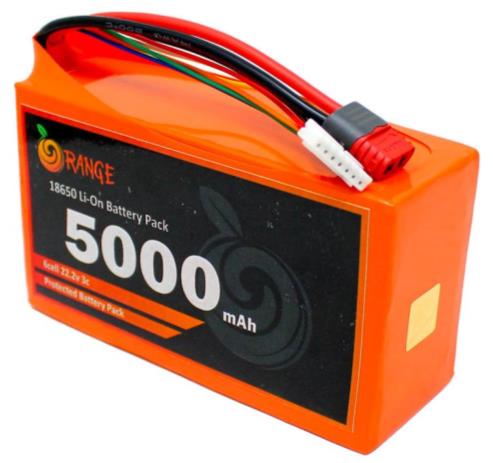
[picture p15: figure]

4. Battery Pack:
i) Model: Orange 18650 Li-ion ii) Nominal Voltage: 22.2 V iii) Max. Charging Voltage: 25.2 V iv) Nominal Capacity: 5000 mAh
v) Max. Discharge Current: 15 A

A battery pack consisting of two 24V 5000 mAh batteries connected in parallel has been chosen for its excellent battery backup. Such a large battery pack is feasible because there is sufficient space inside the robot.

5. Wheel Motor:
i) Johnson Geared Motor (Grade B) ii) Base Motor RPM: 18000
iii) 500 RPM
iv) Rated Torque: 0.1 Nm
v) Stall Torque: 0.48 Nm
vi) Nominal Voltage: 12 V
vii)Operating Range: 6 – 18 V

A geared DC motor with relatively high torque to meet the torque requirement as per the mathematical analysis has been chosen. Since it is a cleaning robot, high robot velocity is not a priority, hence 500 RPM is sufficient.

6. Motor Driver:
i) Double H bridge Drive Chip: L298N 2A ii) Operating Voltage (VDC): 5~35
iii) Peak Current (A): 2
iv) Continuous Current (A): 0-36mA
v) No. of Channels: 2
vi) Can control up to 4 DC Motors

L298N Motor driver has been chosen since it is a very popular choice for robotics projects, and it also meets the design requirements of the robot. It can control up to 4 DC motors, has an inbuilt 5V regulator, and is very cost effective. The robot will use two of these motor drivers – one for the four wheel motors, and one for the two ball screw actuator motors and the vacuum pump motor.

[Figure 6]

[Figure 8]

[Figure 7]

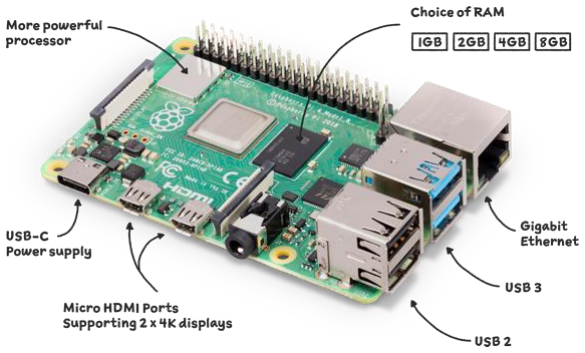
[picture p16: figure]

7. Raspberry Pi 4:

Raspberry Pi 4 Model B 4GB has been chosen because of the complexity of the robot and its various subsystems. A powerful microprocessor is needed to coordinate and execute all the various subsystems in real time.

8. Camera:
i) Model: Raspberry Pi 4 Model B camera module ii) Resolution: 5 MP
iii) Supported Video Formats: 1080p @ 30fps, 720p @ 60fps and 640x480p 60/90 video
iv) Fully compatible with Raspberry Pi 3/4

A Raspberry Pi 4 Model B camera module has been chosen because of its
low cost, and compatibility and ease of integration with the Raspberry Pi 4 Model B microprocessor. A camera module is needed for object detection and to transmit a live video feed via Bluetooth/Wi-Fi.
9. IMU:
i) Model: MPU9250
ii) Accelerometer, Gyroscope & Magnetometer iii) 9 DOF Modules
iv) Power Supply: DC3.3V-5V
v) Chip: MPU9250
vi) Gyro range: ± 250 500 1000 2000 °/s vii)Acceleration range: ± 2 ± 4 ± 8 ± 16g
viii) | Magnetic field range: ± 4800uT

An IMU module has been chosen to fulfil the localization needs of the robot. It has 9DOF and is cost effective.

[Figure 9]

[Figure 10]

[Figure 11]

10. Ball Screw Actuator:
i) Stroke Length: 100 mm
ii) 7 mm/s
iii) Permanent magnet DC motor drive: Voltage 12VDC
iv) Self-Locking Force: 1500N
v) Aluminium frame and extension tube
vi) Long life: A service life of more than
50000 times

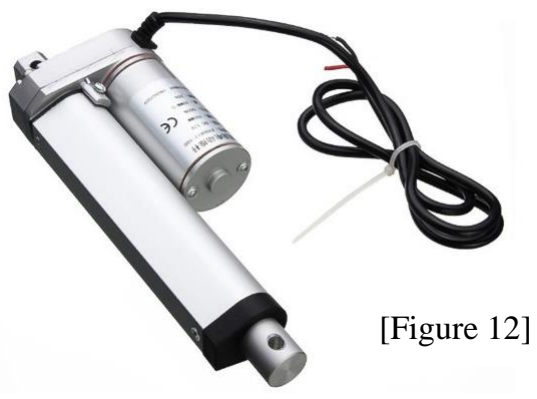
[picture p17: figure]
[Figure 12]

Ball screw linear actuators have been chosen to facilitate the extension and retraction of the robot. The stroke length perfectly matches the project needs, frictional losses are minimal, and controlling it is relatively easy because of DC motors.

11. DC/DC Converters:

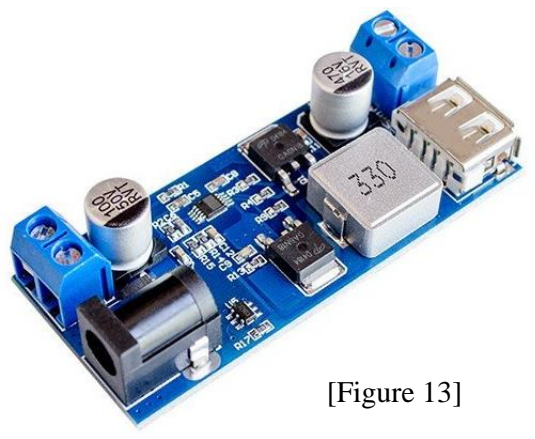
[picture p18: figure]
[Figure 13]
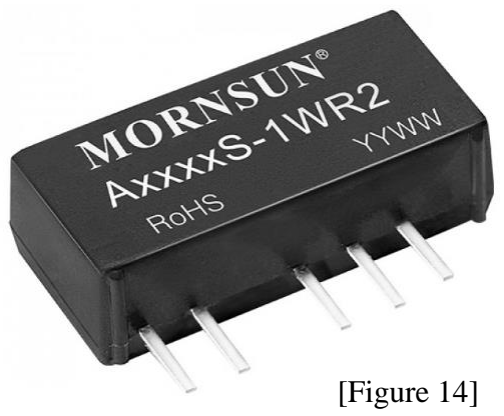
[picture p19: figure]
[Figure 14]

DC/DC converters have been chosen since the robot uses a 24V battery pack. The first DC/DC converted reduces the voltage to 5V for the Raspberry Pi and the on-board sensors. The second one reduces the voltage to 12V for the ball screw actuators and the vacuum pump.

i) Working voltage: DC 9V–36V
ii) Output voltage: 5.2V/5A/25W i) 24V to 12V DC -DC Converter ii) High efficiency of up to 80%

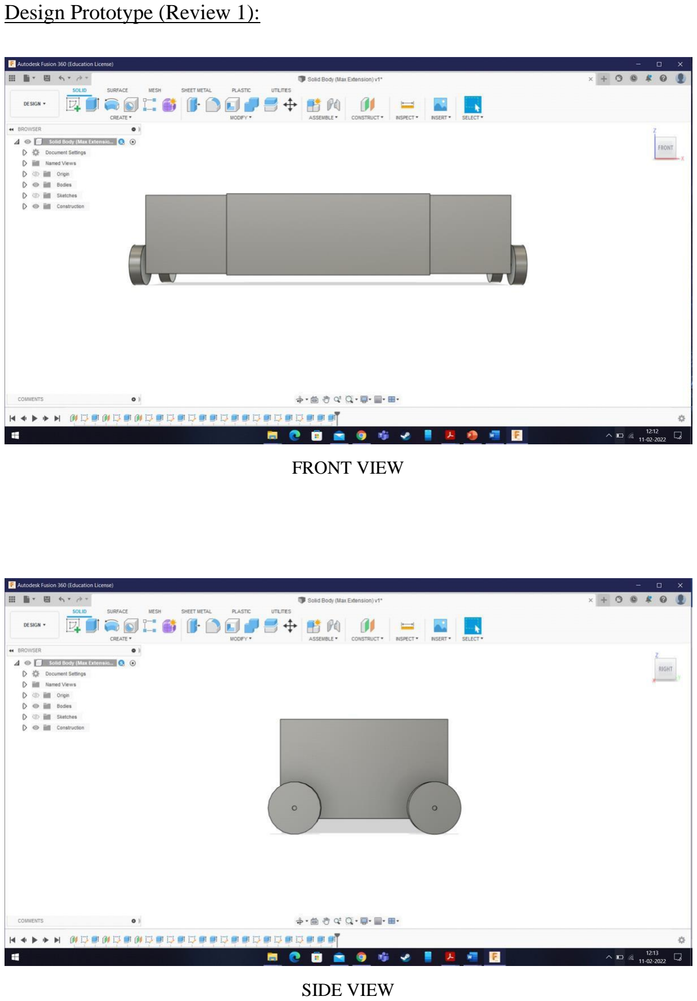
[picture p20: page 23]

### Design Prototype (Review 1):

FRONT VIEW

SIDE VIEW


TOP VIEW

ISOMETRIC VIEW

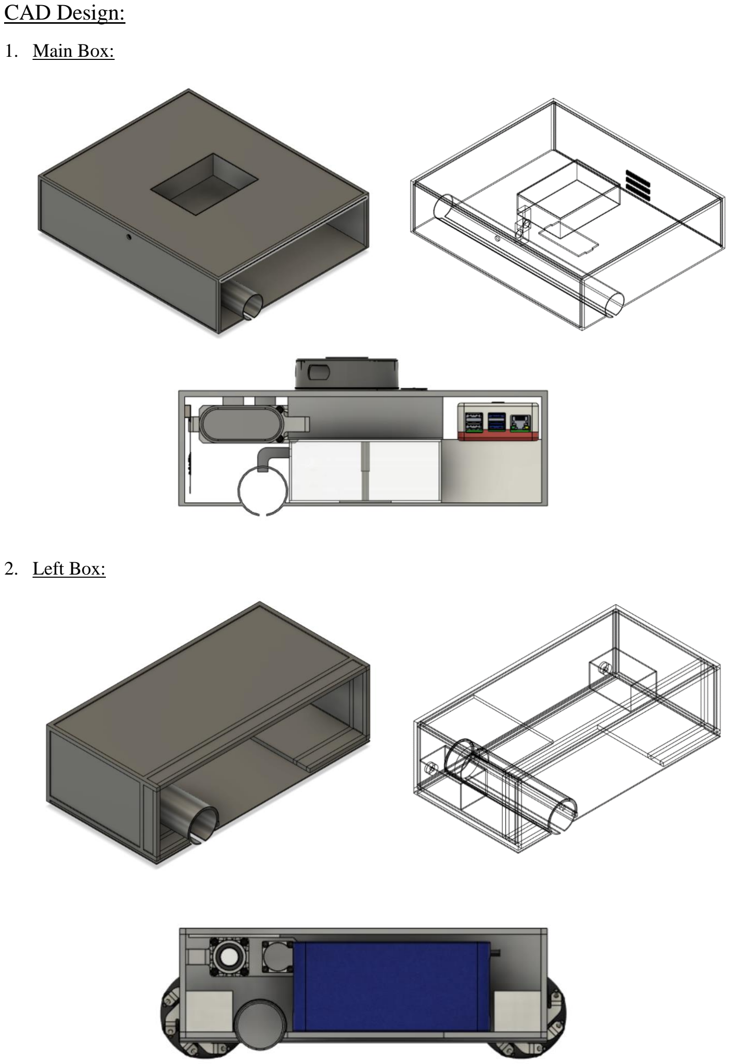
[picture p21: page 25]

### CAD Design:

1. Main Box:
2. Left Box:

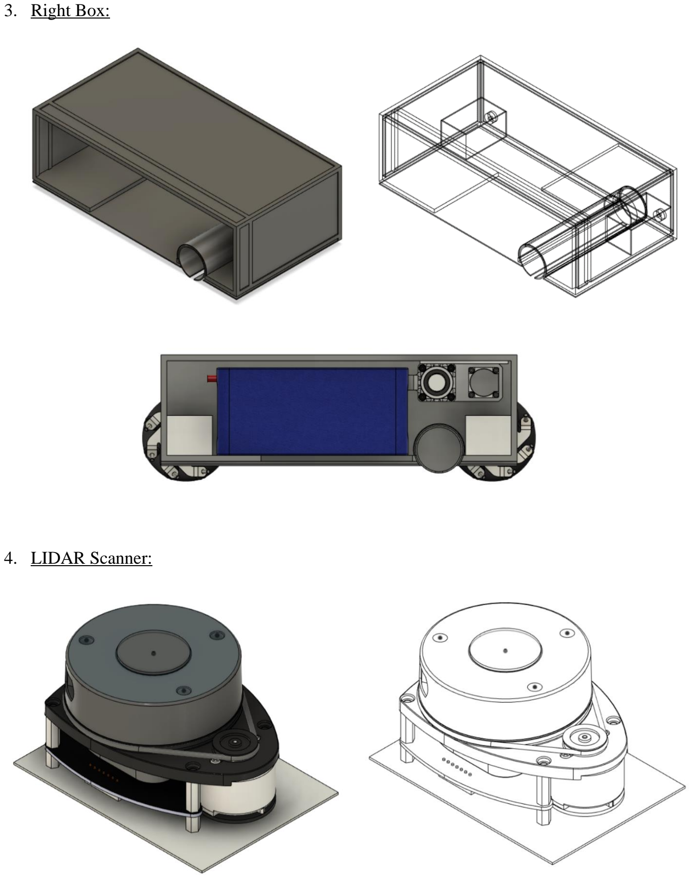
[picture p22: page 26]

3. Right Box:
4. LIDAR Scanner:

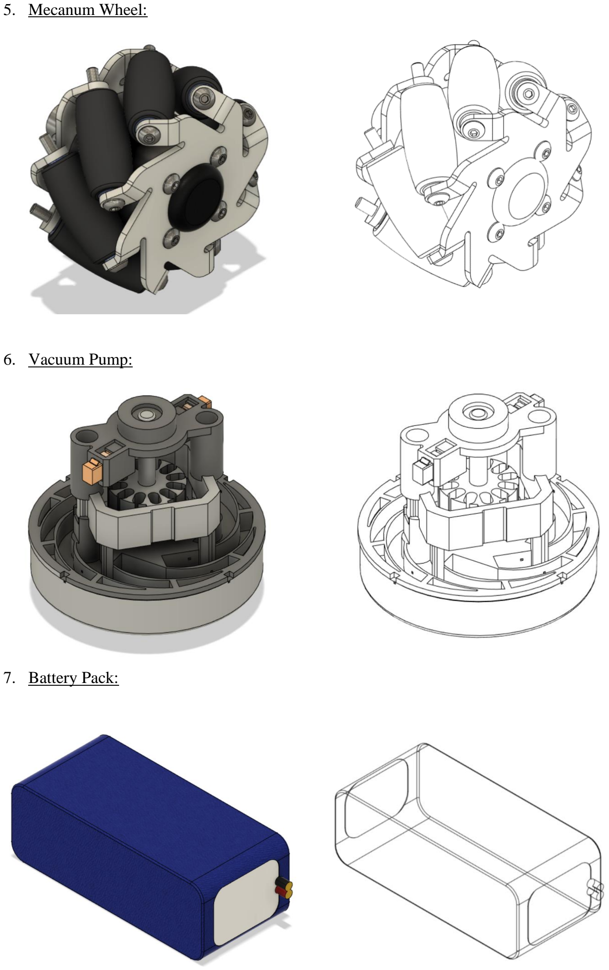
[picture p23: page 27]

5. Mecanum Wheel:
6. Vacuum Pump:
7. Battery Pack:

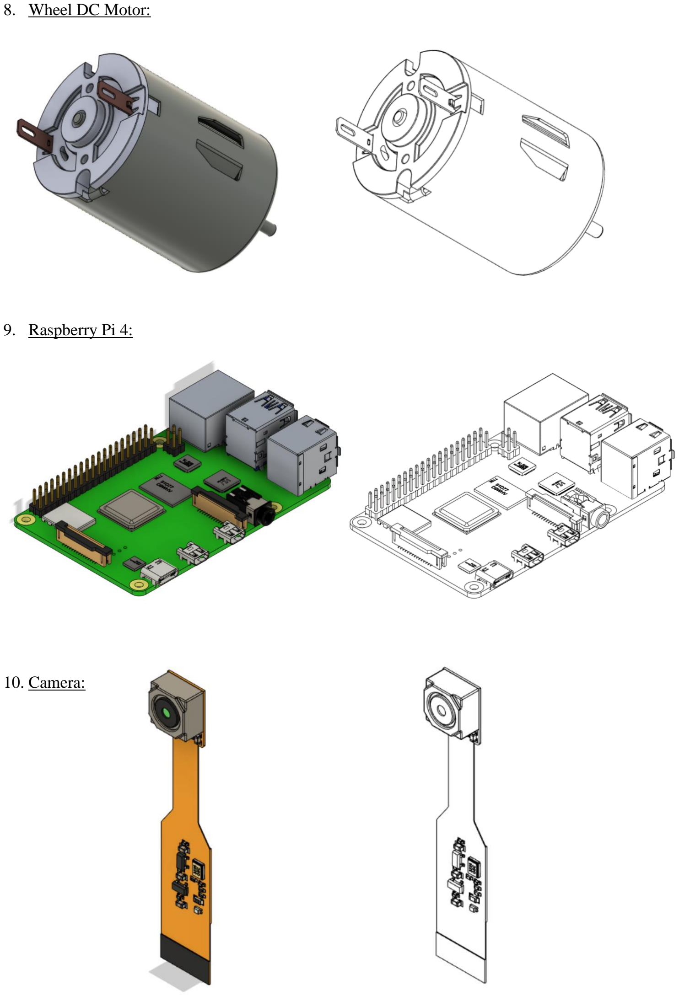
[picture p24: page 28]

8. Wheel DC Motor:
9. Raspberry Pi 4:
10. Camera:

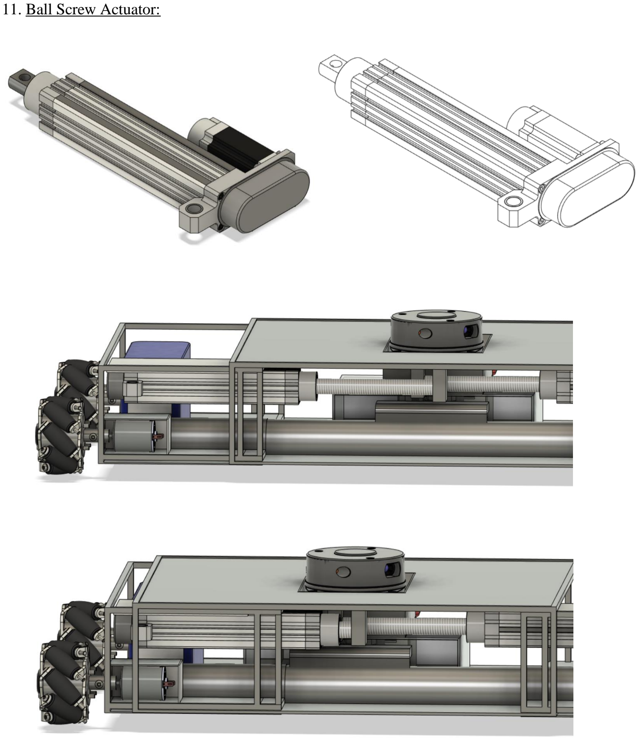
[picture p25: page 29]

11. Ball Screw Actuator:

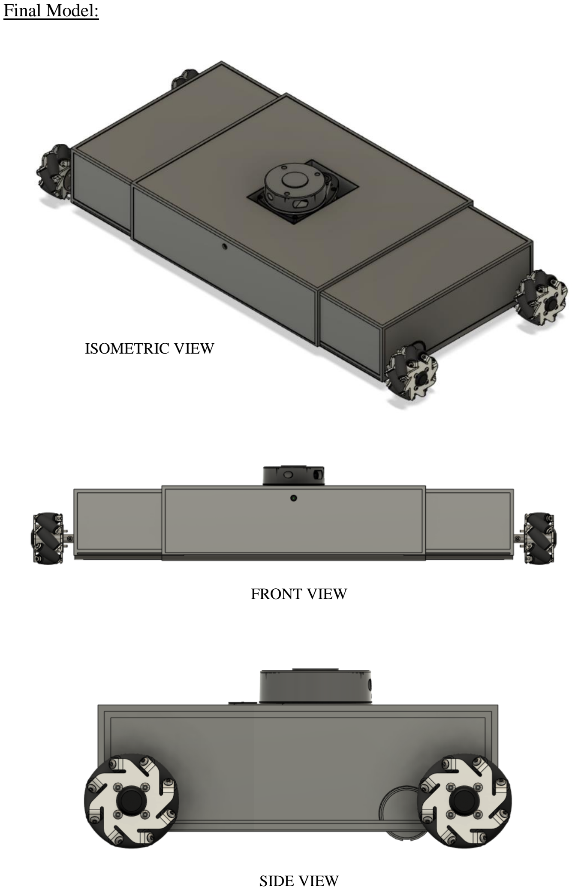
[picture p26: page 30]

### Final Model:

ISOMETRIC VIEW

FRONT VIEW

SIDE VIEW

TOP VIEW

BOTTOM VIEW

BACK VIEW


Maximum Length

Minimum Length


### Simulation:

A simulation study has been created to demonstrate and analyse the efficacy and effectiveness of the system. A simplified CAD model has been developed to ensure that the simulation goes smoothly. The CAD model has further been exported as a URDF file, and then imported into the simulation software. The simulation software chosen is CoppeliaSim (V-REP) because of its simplicity and familiarity with the software. Further, the joints and links have been defined, sensors integrated, and the scene set. The robot is able to move and also change its size effectively.

https://drive.google.com/file/d/19EQk5tqUa7tWNCU656DGSFBoZz20wXNN/view?usp=sh aring (https://drive.google.com/file/d/19EQk5tqUa7tWNCU656DGSFBoZz20wXNN/view?usp=sharing)

### Work to be Done:

1. Integration of SLAM and object detection using LIDAR and camera- Simultaneous Localization and Mapping will be used by the cleaning robot to create a map of the terrain and the concept of Light Detection and Ranging is used which collects information about variable distances between the robot and an obstruction using light in the form of a pulsed laser.
2. Development of the control system for the Mecanum wheels, and for actuating the Ball Screw Linear Actuator for changing the size (length) of the robot.
3. Integration of Dijkstra algorithm for path planning, along with object detection.
4. Conduction of a Simulation study to demonstrate the efficacy of the system.
5. Conduction of Stress Analysis on the robot.

### Gantt Chart:


### Milestones in the Project Phase:

1. Completion of Chassis Design
2. Development of CAD Design for Actuation Mechanism
3. Development of Path Planning Algorithm
4. Development of Object Detection Algorithm
5. Development of the control system to actuate the Ball Screw Linear Actuator used to change the size of the robot
6. Conduction of Simulation study

### Summary:

Cleaning robots have advanced significantly in recent years, owing to increased market presence and the demand for improved cleaning performance. However, due to geometric restrictions of the platforms in relation to the cleaning stage, as well as furniture and architecture, most robots have difficulty covering the whole cleaning area. The aim is to use the on-board sensors which will mainly be used for SLAM (Simultaneous Localization and Mapping) integrated using LIDAR and camera to detect obstacles and change the robot configuration accordingly and to navigate forward and backward and even sideways with the

15-Jan | 04-Feb | 24-Feb | 16-Mar | 05-Apr

Literature Review

Design Planning

Computer Aided Design

Coding

Integrating Everything

Simulation

| Everything Simulation | | Aided Design Coding Integrating | | Literature Review Design Planning Computer
Start Date | 01-Apr | 20-Mar | 25-Feb | 15-Feb | 10-Feb | 15-Jan
Days to Complete | 20 | 10 | 28 | 28 | 5 | 26

### Gantt Chart

help of Mecanum wheels. The plan is to use a ball screw actuation mechanism to change the length of the robot according to what it maps about the local terrain using the sensors. A precise CAD model will be designed with parameters so as to bring down cost of making the cleaning robot to the bare minimum while also optimizing its cleaning efficiency at the same time.

From the CAD design point of view, the robot comprises 3 hollow cuboid compartments that overlap and can linearly actuate with the help of the ball screw mechanism. The vacuum system comprises a set of rigid concentric pipes, and there will be a slit along the length of the pipe which will make the vacuum opening. The ends of these pipes will be attached to the walls of the robot on both sides. Hence, whenever the pipes will move further away from each other the slit opening will also increase making it more efficient to collect dust. These pipes will be connected to a storage compartment via a connecting pipe.

Increasing the area of the vacuum opening will reduce the suction power so to overcome this problem a motor will be inserted which will adjust the suction power based on the largest opening. For example, when the robot is fully extended it will be powerful enough to absorb dust at the largest opening and when the opening size reduces i.e., when the robot contracts, the vacuum motor voltage will automatically be reduced using a buck converter in order to maintain a constant suction pressure.

### References:

[1] E. Prassler, A. Ritter, C. Schaeffer and P. Fiorini, “A Short History of Cleaning Robots,” Autonomous Robots, vol. 9, pp. 211-226, December 2000.
[2] H. Endres, W. Feiten and G. Lawitzky, “Field Test of a Navigation System: Autonomous Cleaning in Supermarkets,” IEEE International Conference on Robotics and Automation , 06 August 2002.
[3] N. Kushal, H. Chaudhuri and H. Nikithesh, “Autonomous Floor Cleaning Bot,” International Research Journal of Engineering and Technology (IRJET), vol. 5, no. 6, June 2018.
[4] S. Kim, “Autonomous Cleaning Robot: Roboking System Integration and Overview,” IEEE International Conference on Robotics and Automation, 07 June 2004.
[5] Y. Liu, S. Zhu, B. Jin, S. Feng and H. Gong, “Sensory Navigation of Autonomous Cleaning Robots,” Fifth World Congress on Intelligent Control and Automation, 18 October 2004.
[6] K. Hasan, A. Nahid and K. Reza, “Path Planning Algorithm Development for Autonomous Vacuum Cleaner Robots,” 2014 International Conference on Informatics, Electronics & Vision (ICIEV), May 2014.

[7] A. Joon and W. Kowalczyk, “Design of Autonomous Mobile Robot for Cleaning in the Environment with Obstacles,” Applied Science 2021, vol. 11, no. 17, p. 8076, 31 August 2021.
[8] S. Hossen, R. Shaharear, F. Islam, S. Islam, N. Hossain and S. Datta, “Designing and Optimization of An Autonomous Vacuum Floor Cleaning Robot,” in 2019 IEEE International Conference on Robotics, Automation, Artificial-intelligence and Internet-of-Things (RAAICON), November 2019.
[9] L. Gerstmayr-Hillen, F. Röben and M. Krzykawski, “Dense Topological Maps and Partial Pose Estimation for Visual Control of An Autonomous Cleaning Robot,” Robotics and Autonomous Systems, vol. 61, no. 5, May 2013.
[10] K. Karur, N. Sharma, C. Dharmatti and J. Siegel, “A Survey of Path Planning Algorithms for Mobile Robots,” Electrified Intelligent Transportation Systems, vol. 3, no. 3, pp. 448-468, 04 August 2021.
[11] M. Dakulović, S. Horvatić and I. Petrović, “Complete Coverage D* Algorithm for Path Planning of a Floor-Cleaning Mobile Robot,” IFAC Proceedings Volumes, vol. 44, no. 1, pp. 5950-5955, January 2011.
[12] C. Lamini, S. Benhlima and A. Elbekri, “Genetic Algorithm Based Approach for Autonomous Mobile Robot Path Planning,” Procedia Computer Science, vol. 127, pp. 180-189, 2018.
[13] M. Yakoubi and M. Laskri, “The Path Planning of Cleaner Robot for Coverage Region Using Genetic Algorithms,” Journal of Innovation in Digital Ecosystems, vol. 3, no. 1, pp. 37-43, June 2016.
[14] Y. Liu, X. Lin and S. Zhu, “Combined Coverage Path Planning for Autonomous Cleaning Robots in Unstructured Environments,” 2008 7th World Congress on Intelligent Control and Automation, 08 August 2008.
[15] C. Hofner and G. Schmidt, “Path Planning and Guidance Techniques for An Autonomous Mobile Cleaning Robot,” Robotics and Autonomous Systems, vol. 14, no. 2-3, pp. 199-212, May 1995.
[16] B. Ramalingam, A. Lakshmanan, M. Ilyas, A. Le and M. Elara, “Cascaded Machine-Learning Technique for Debris Classification in Floor-Cleaning Robot Application,” Applied Science 2018, vol. 8, no. 12, p. 2649, 17 December 2018.
[17] G. Schmidt and C. Hofner, “An Advanced Planning and Navigation Approach for Autonomous Cleaning Robot Operations,” International Conference on Intelligent Robots and Systems, 06 August 2002.
[18] R. Parween, M. Heredia, M. Rayguru and R. Abdulkader, “Autonomous Self-Reconfigurable Floor Cleaning Robot,” IEEE, pp. 114433-114442, 01 June 2020.

[19] R. Parween, V. Prabakaran, M. Elara and A. Vengadesh, “Application of Tiling Theory for Path Planning Strategy in a Polyiamond Inspired Reconfigurable Robot,” IEEE, pp. 6947-6957, 18 December 2018.
[20] J. Forlizzi and C. DiSalvo, “Service Robots in The Domestic Environment: A Study of The Roomba Vacuum in The Home,” HRI 06': Proceedings of the 1st ACM SIGCHI/SIGART Conference on Human-Robot Interaction, pp. 258-265, 02 March 2006.
[21] P. Eng, B. Laurean and D. Telea, “Management and Motion Control of Ball Screw Actuators Applied in the Robotic Structures,” Control Systems Engineering, June 2012.
[22] S. Bhowmick, R. Adhikari and S. Dutta, “Practical Applications for Mobile Robots based on Mecanum Wheels - A Systematic Survey,” IJIREEICE, vol. 6, no. 12, pp. 20-24, December 2018.
[23] M. Zhao, H. Lu, S. Yang, Y. Guo and F. Guo, “A Fast Robot Path Planning Algorithm Based on Bidirectional Associative Learning,” Computers & Industrial Engineering, vol. 155, p. 107173.
[24] A. Lakshmanan, R. Mohan, B. Ramalingam, A. Le, P. Veerajagadeshwar, K. Tiwari and
M. Ilyas, “Complete Coverage Path Planning Using Reinforcement Learning for Tetromino Based Cleaning and Maintenance Robot,” Automation in Construction, vol. 122, p. 103078, April 2020.
[25] Z. Yan, S. Schreiberhuber, G. Halmetschlager, T. Duckett, M. Vincze and N. Bellotto, “Robot Perception of Static and Dynamic Objects with An Autonomous Floor Scrubber,” Intelligent Service Robotics, pp. 403-417, 08 June 2020.
[26] H. Wang, Y. Yu and Q. Yuan, “Application Of Dijkstra Algorithm in Robot Path-Planning,” IEEE, 18 August 2011.
[27] L. Yang, J. Qi, D. Song, J. Xiao, J. Han and Y. Xia, “Survey of Robot 3D Path Planning Algorithms,” Journal of Control Science and Engineering, vol. 2016, no. Article ID 7426913, 04 July 2016.
[28] M. Elara, N. Rojas and A. Chua, “Design Principles for Robot Inclusive Spaces: A Case Study with Roomba,” IEEE, 29 September 2014.
[29] J. Jones, “Robots At the Tipping Point: The Road to iRobot Roomba,” IEEE, pp. 76-78, 2006 February 2006.
[30] Gross and Jennifer, “Interviewing Roomba: A Posthuman Study of Humans and Robot Vacuum Cleaners,” Explorations in Media Ecology, vol. 19, no. 3, pp. 285-297, 01 September 2020.
[31] B. Tribelhorn and Z. Dodds, “Evaluating The Roomba: A Low-Cost, Ubiquitous Platform for Robotics Research and Education,” IEEE, 21 May 2007.

[32] Bergman and Joel, “Robot Vaccum Cleaner,” School of Industrial Engineering and Management (ITM), p. 70, 2019.
[33] T. Asafa, T. Afonja, E. Olaniyan and H. Alade, “Development of a Vacuum Cleaner Robot,” Alexandria Engineering Journal, vol. 57, no. 4, pp. 2911-2920.
[34] Z. Zhang and Z. Zhao, “A Multiple Mobile Robots Path Planning Algorithm Based on A-Star and Dijkstra Algorithm,” International Journal of Smart Home, vol. 8, no. 3, pp. 75-86, May 2014.
[35] N. Buniyamin, W. Ngah, N. Sariff and Z. Mohamad, “A Simple Local Path Planning Algorithm for Autonomous Mobile Robots,” Control Systems Engineering, January 2011.
[36] M. Elara, N. Rojas and A. Chua, “Design Principles for Robot Inclusive Spaces: A Case Study with Roomba,” 2014 IEEE International Conference on Robotics and Automation (ICRA), 29 September 2014.
[37] P. Adithya, R. Tejas, S. Varun and B. Prashanth, “Design and Development of Automatic Cleaning and Mopping Robot,” IOP Conference Series: Materials Science and Engineering, vol. 577, no. 012126, 16 August 2018.
[38] M. Ilyas, S. Yuyao, R. Mohan, M. Devarassu and M. Kalimuthu, “Design of sTetro: A Modular, Reconfigurable, and Autonomous Staircase Cleaning Robot,” Journal of Sensors, vol. 2018, no. Article ID 8190802, 24 July 2018.
[39] T. Ichimura and S.-i. Nakajima, “Development of an autonomous beach cleaning robot “Hirottaro”,” 2016 IEEE International Conference on Mechatronics and Automation, 05 September 2016.
[40] V. N. Shah, Sathvik and A. Vaghela, “Floor Cleaning Robot (Autonomus/Manual),” International Journal of Engineering Research & Technology (IJERT), no. 2016.
[41] V. Silva, J. Roche and A. Kondoz, “Robust Fusion of LiDAR and Wide-Angle Camera Data for Autonomous Mobile Robots,” Sensors 2018, Depth Sensors and 3D Vision, vol. 18, no. 8, p. 2730, 20 August 2018.
[42] C. E. O. Lima and S. Sano, “Design and Analysis of a New Type of Mecanum Wheel,” in Proceedings of 175th IASTEM International Conference – Tokyo, Japan, April 2019.

### References (Figures):

1. https://www.slamtec.com/en/Lidar/A1
2. https://robu.in/product/60mm-aluminium-lego-compatible-mecanum-wheels-set-2-left-2-right/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 (https://robu.in/product/60mm-aluminium-lego-compatible-mecanum-wheels-set-2-left-2-right/)

3. https://www.nidec.com/en/product/search/category/B101/M111/S103/NCJ-G10D12BS2AZ-0/ (https://www.nidec.com/en/product/search/category/B101/M111/S103/NCJ-G10D12BS2AZ-0/)
4. https://robu.in/product/orange-18650-li-ion-5000mah-6s-22-2v-3c-6s2p/?gclid=Cj0KCQjw5-
WRBhCKARIsAAId9Fku_lrJBJEDVFC5g0G3dXgx27NNzE6Mnec0wvolu_dZ3oA4Vg O4NtgaAhJUEALw_wcB (https://robu.in/product/orange-18650-li-ion-5000mah-6s-22-2v-3c-6s2p/)
5. https://robu.in/product/johnson-motor-made-india-500-rpm/
6. https://robu.in/product/l298n-2a-based-motor-driver-module-good-quality/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 (https://robu.in/product/l298n-2a-based-motor-driver-module-good-quality/)
7. https://www.raspberrypi.com/products/raspberry-pi-4-model-b/
8. https://no.rs-online.com/web/p/raspberry-pi-cameras/9132664
9. https://robu.in/product/mpu9250-9-axis-attitude-gyro-accelerator-magnetometer-sensor-module/ (https://robu.in/product/mpu9250-9-axis-attitude-gyro-accelerator-magnetometer-sensor-module/)
10. https://robu.in/product/linear-actuator-stroke-length-100mm7mm-s1500n12v/
11. https://robu.in/product/24v-12v-to-5v-5a-power-module-dc-dc-xy-3606-power-converter/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 (https://robu.in/product/24v-12v-to-5v-5a-power-module-dc-dc-xy-3606-power-converter/)
12. https://www.electronicscomp.com/a2412s-1wr2-mornsun-24v-to-12v-dc-dc-converter-1w-power-supply-module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 (https://www.electronicscomp.com/a2412s-1wr2-mornsun-24v-to-12v-dc-dc-converter-1w-power-supply-module)

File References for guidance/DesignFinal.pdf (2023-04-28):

ME 423 ENGINEERING DESIGN VII

PHASE III – FINAL PROPOSAL & DESIGN

### Robovac (Autonomous Robotic Vacuum Cleaner)


A SENIOR REPORT

ME 423 GROUP 1
Juan Gamarra
Diego Molina
Jetmir Palushi
Raymond Perez
Joseph Seborowski

ADVISOR: Jae Chung

STEVENS INSTITUTE OF TECHNOLOGY Castle Point on Hudson
Hoboken, NJ 07030

December 7, 2006

Table of Contents

Project background | | 4
Objective and Mission statement | | 5
Conceptual Designs | | 6
State of the Art Improvements | | 7
Reshaping | | 7
Mapping | | 8
Sensors | | 9
Dirt | | 9
Obstacle | | 9
Incline/Decline | | 10
Mapping | | 10
Programming | | 11
Total Cost of Sensors | | 11
Power Consumption | | 11
Design | | 12
Case Optimization | | 12
Brush Optimization | | 13
Battery | | 13
Selected Battery | | 15
Motors | | 16
Blowers | | 17
Gears | | 17
Power loss due to friction | | 18
Cleaning | | 18
Appendix | | 21
Figure 1 Stair Cleaner | | 21
Figure 2 Water Filtration | | 22
Figure 3 Dirt Sensosr | | 23
Figure 4 RF Transmitter/Encoder | | 24
Figure 5 Sharp Engine Card | | 24
Figure 6 Algorithm | | 25
Figure 7 Von Mises Stress | | 30
Figure 8 Mass and Volume Optimization | 31
Figure 9 Final Bottom Piece | | 32
Figure 10 Brush Optimization | | 33
Figure 11 Brush Configuration | | 34
Figure 12 Infrared Sensors | | 35
Figure 13 Bumper | | 35
Figure 14 Motor Mount | | 36
Figure 15 Microcontroller | | 37
Figure 16 Battery | | 38
Figure 17 Blower | | 39
Figure 18 Display Screen | | 40
Figure 19 Wireless Transmitter | | 41

Figure 20 Battery Analysis | | 42
Figure 21 Main Brushes | | 43
Figure 22 Gear Efficiencies | | 43
Figure 23 Suction Motor | | 44
Figure 24 Dusk Bin | | 45
Figure 25 Reynolds Number, Velocities, Densities, and Pressure | 46
Figure 26 Steam Version of System | 46
Figure 27 Flow Rate | | 47
Figure 28 Compressibility Factor | | 47
Figure 29 Steam Heat Capacity Ratio | 48
Figure 30 Selection of Materials, Piping | 48
Figure 31 Absolute Roughness | 49
Figure 32 Minor Loss due to Flush Entrances | 49
Figure 33 Minor Loss due to Exhaust Port | 50
Figure 34 Minor Loss due to Stab in Type Branch | 50
Figure 35 Losses due to two 90 Degree Bends | 51
Figure 36 Calculations | | 52

Project Background

The first Roomba was thirteen inches in diameter and roughly four inches high. The Roomba used a large bumper mounted on the front of the unit to detect any walls or objects in its path. The robot was equipped with infrared sensors on the top front center. It also used a virtual wall that transmitted infrared to the unit so it does not attempt to clean other rooms and get lost.

The first prototype consisted of three settings. The settings consisted of setting a room size, small, medium and large. Roomba’s first feature at the time was the ability to detect whether or not there was enough power for it to clean the room size you chose. However as technology has gotten more sophisticated so has the Roomba. The Roomba can now detect room sizes without a user input.

The first Roomba operated on internal nickel metal hydride batteries that required being recharged regularly from a wall plug. The newest generations of Roomba’s now have self charging features. The Roomba takes about six to eight hours to recharge itself. iRobot offers a fast recharging pack which can recharge in 3 hours at the price of $60.

The newer generations Roomba’s are virtually completely automated. The user has to just place the Roomba on the floor and choose clean, spot, or max. The clean button will clean a room. Spot clean will clean an area. Max will clean until the battery runs out. The Roomba also now has an automatic scheduler accessory.

Electrolux Trilobite and Samsungs robots now have the ability to map out rooms they are cleaning. Roomba, unlike Electrolux Trilobite, relies on simple algorithms such as spiral cleaning.

An MIT researcher and iRobot CTO Rodney Brooks’ philosophy that robots should be like insects, equipped with simple control mechanisms tuned to their environments. The result is that although Roombas are effective at cleaning rooms, they take several times as long to do the job as a person would, usually covering some areas many times and other only once or occasionally not at all.¹

1
http://en.wikipedia.org/wiki/Roomba

Objective

Identify and design an autonomous robot that will assist people at home who are too busy for daily or weekly floor cleaning, especially for family’s with children. In particular for the elderly who live by themselves and do not have the strength or ability to clean. Robotic vacuum cleaners in the market are expensive and inefficient in terms of cleaning time and cleanness. The goal is to design an omni directional platform with infrared sensors, wireless sensors, bumpers, ultrasound, reshape, and four bristle brushes on every side to improve the cited cleaning performance problems.²

Mission Statement: Robotic Vacuum Cleaner
Product Description | • Omni directional, cleans efficiently, uses infrared sensors, self charging, bumpers, wireless, ultrasound, reshape
Key Business Goals | • Environmentally friendly • Be the leader in economic robotic vacuum cleaners • First prototype to released in mid April • Product introduced in fourth quarter December 2007 • Capture 20% of robotic vacuum cleaner sales by 2009 • First product serves as a platform for high end robotic vacuum cleaners • Include a two year full warranty with every vacuum sold
Primary Markets | • New robotic vacuum cleaner users • Middle – class families ($25,000-$100,000) • Average size homes (2300 sq. ft.)
Secondary Markets | • Existing robotic vacuum cleaner motor • Professional cleaning services • Schools, businesses • Upper class families ($100,000 – unsp.)
Assumptions and Constraints | • New product platform • Rechargeable battery technology • Self charging • Self docking • Infrared system • Wireless system • Some devices and parts will be manufactured outside of the United States to meet the sales objective
Stakeholders | • Purchasers and users • Manufacturing operations • Service operations • Distributors and resellers • Sales force

2
ME 423 Mechanical Engineering Design VII Project Descriptions Fall 2006

Conceptual Designs

All robotic vacuum cleaners that are out in the market today are disk shaped. The problem with that is that they cannot clean the corners of rooms very well. Since our main objective was to improve the overall cleaning efficiency, we decided to change the shape from a circle to a square. The square design will allow our vacuum to clean the corners of rooms better.


Disk Shaped Design | Redesigned Square Shaped

One of our first ideas was to make our vacuum able to clean stairs since no robotic vacuum out in the market today does that. The vacuum would be able to hoist itself up the stairs and clean each stair. We got rid of this design because it did not meet any of our customer needs or concerns. Figure 1 in Appendix

A customer concern was the dusk bin. You had to remove and empty out the dusk bin yourself once the vacuum was done cleaning. The dusk wasn’t sealed well in the bin and when you would take it out of the vacuum, if you were not careful the dusk would come out of the bin and fall on the carpet. To prevent this from happening, an idea was to make a water filtration system. The dirty air would pass through the water and the HEPA filter and come out as clean air. This design didn’t workout because we weren’t sure if we can completely contain the water and not allow the water to escape and go into the electrical systems of the vacuum. Figure 2 in Appendix

State of the art review and improvements:

Based on the information gathered the team broke down the areas of improvement to five Sections: Shape, Sensors, Batteries, Suction, and Motors. Below we will examine the technology and state of the art aspects of the Robovac as opposed the competitors which were researched.

Reshaping

The typical shape of a robotic vacuum cleaner is a disk. The reasons they are disk-shaped is because of mobility. They can maneuver through tight spaces and still clean effectively. When they bump into a wall or piece of furniture, since it is a circle, it can easily turn around and adjust its position and continue cleaning. The major problem with the vacuum being a circle is that it cannot clean the corners of rooms very well. If you change the shape to a square, then the vacuum can get into the corners and clean better, but there are no square robot vacuums. The reason why there are no square vacuums is because of the pointed edges. As the vacuum is going along and cleaning it will bump into obstacles and then re-position itself. As the vacuum is re-positioning itself, the edges can come into contact with obstacles and will waste more time re-positioning itself instead of cleaning. Our new design for the shape of the vacuum is going to be a square with rounded edges.

Having a square will get the corners to be cleaned much better and the rounded edges will allow the vacuum to have the same mobility to work its way through tight spots. We will be compromising some mobility in changing the shape to a square with rounded edges. The circle shaped vacuums right now can easily readjust when it comes in contact with an obstacle especially in tight spots. If the vacuum is cleaning under a chair with 4 legs, a circle shaped vacuum can make its way under the chair and clean around the legs without much difficulty. The same goes for table, couch and bed legs. The corners of a room don’t even get cleaned because it can’t get into the corners all the way before bumping into the wall.

The square shaped with rounded edges will be able to clean corners better and also along walls. The only drawback is that it will lose some mobility and maneuverability. It is impossible to be able to make the robot clean corners 100%. It will never be able to clean corners and along walls perfectly. Having a square with rounded edges is the best design for our vacuum. It will be able to clean corners and along walls better then a circle shaped vacuum. We want to keep the area of the square vacuum about the same as the circle.

Also, keeping it the same height as the Roomba will allow our vacuum to clean under most beds, chairs and couches. The height of couches, beds, desks, etc, varies in size. The vacuum will either be able to or won’t be able to clean under them. The height of the furniture off the ground is about an inch from the ground or as much as 6 inches from the ground. If the vacuum is able to get under the couch or bed, it probably won’t get stuck under there. It should be able to make its way underneath the furniture, clean and then get out from under there without a problem.

Keeping it roughly the same area and height of today’s robot vacuums will allow it to clean under furniture. The cleaning equipment and wheels will be able to fit inside the square shape with no problems. Adjustments will need to be made as to where the brushes, wheels and vacuum need to placed.

Most robotic vacuum cleaners are made out of hard plastic. Customers are worried about the longevity of the product. The plastic edge bumps into furniture and walls frequently. The plastic that we are going to use is acrylonitrile butadiene styrene. ABS is a thermoplastic used to make light, rigid, molded products and is known for its resistance, toughness and electrical insulation properties. ABS is commonly used in the electrical and electronics industries because it is not only highly scratch and wear resistant but also decorative and easy to maintain. The cost of producing ABS is roughly twice the cost of producing polystyrene, but is worth it due to its hardness.

Mapping
One of the major disadvantages of the current robots is that in order to find the way back to the battery charger, the battery charger must be located to the wall or else the robot won't be able to charge itself in an automated fashion. Even when the charger is right on the wall the robot will still miss the battery charger in some cases because its coordinates have deviated while it was cleaning the room. On the other hand we plan to improve our robot, the RoboVak, by introducing a totally different concept from the current technology that is being used in market. Our technology will allow us to place the battery charger anywhere on the room and it is guaranteed that the robot will find the charging location. Our team came up with several ideas:
1) Keeping track of the coordinates while the robot is cleaning the room and use these coordinates to track back the path when the robot needs to be charged.
2) Use a random algorithm to approximate the location of the battery charger, and use sensors to find the exact location.
3) Use a wireless system that will keep track of the location of the battery charger so the robot can find it in a finite time when it needs to be recharged.
4) Use directional radio antennas between the robot and the home to guide the robot on the direction of the battery charger.
Idea number two was eliminated for the following reasons:
a) It takes a long time for the robot to find the charger and the battery might be completely discharged before the robot locates the home.
b) It does not increase the probability of finding the home more frequently than the current products.
The other three ideas were picked for further evaluation.

Sensors

Dirt Sensors Figure 3 in Appendix
The reason why we must be able to detect the amount of dirt entering the vacuum is because dirtier areas must be cleaned for a longer time. If we do not clean these dirtier areas longer by decreasing the speed of the vacuum than the room will not be completely cleaned at the end of the cleaning procedure.
There are two potential ideas how to detect the amount of dirt entering the suction. First one is to use an ultrasonic sensor. Basically we mount two sensors on the opposite sides at the dirt entrance and monitor the amount of dirt using a voltmeter circuit. See the diagram below for schematics. The other idea is to use a wrap a piece of wire around the suction in the form of a solenoid and monitor the electric field induced on this solenoid. The dirt content will change the conduction of the electromagnetic field inside of the solenoid and therefore we can detect higher content of dirt from lower ones.

Obstacle Sensors
Since most of the sensors our team researched would measure either very close distances or greater than 2" we decided that the best way to go for detecting the wall and other obstacles that the robot will hit is using microscopic bumpers which can be small and any shape we want them to be in order to minimize the amount of space on the robot. The circuit diagram of a bumper is given below:

Circuit representation of the bumper switch

The bumper is represented by the open switch (S1) meaning that the robot hasn't hit anything. When the bumper is closed the current starts to flow from -5V to Ground therefore the digital input will change its value from logic 0 to logic 1 and the software will detect an obstacle and proceed to another loop and try to eliminate whatever the robot has hit. Building this circuit will cost approximately 1$.

Rapid Incline/Decline sensors

Sharp GP2Y0A21YK infrared sensor Detects distance from 10cm-80cm. This infrared can be used to detect the stairs and steep inclines, when there is a sudden changed on the height from where the sensor is mounted to the floor. The only concern is that the distance from the floor to the sensor must be equal or greater than 4" for this sensor to work accurately. The sharp GP2Y0A21YK is priced at 10$.

Mapping sensors

RF transmitter/receiver + light sensors to guide the robot when it runs out of battery

Pre-made Transmitter
Operates in excess of 300feet, a receiver of this kind can be purchased for decoding the encoded digital signal on the analog wave. Easy to install, and very small so it can be mounted anywhere on the body of the robot. The only part needed is the antenna. This sensor transmitter is priced at 16.66$. Figure 4 in Appendix

Programming

The schematic below shows how all the sensors are integrated on the programmed printed circuit board.

The fact that we have so many sensors to facilitate the navigation of the robot we had to select a microcontroller that had a lot of general purpose input/output pins. These pins will be used to hook up all the sensor inputs to monitor their voltage or current drop. The most feasible card for the RoboVAC project seemed the Sharp Engine Card that has 64 I/O pins and meets our requirements. A diagram of the card. Figure 6 in Appendix
The algorithm can be seen in Figure 6 of the Appendix.
Total Cost of Sensors for mapping
Quantity | Sensor | Price
1 | Polaroid Sensor | 19$
10 | Bumper Switches | 10$
5 | Sharp Infrared | 50$
2 | RF transmitter/receiver | 64$
TOTAL | 143$

Power Consumption

Sensor | Power/Sensor | Total
Wall Bumpers | 25mW | 0.2W
Infrared | 175mW | 0.7W
Dirt | 10mW | 0.01W
Wireless | 7.5mW | 15mW
TOTAL | 0.925W

Design

Case Optimization:
The material being used for the case and most of the robot is ABS because it is easily manufactured, cheap and it can be injection molded. Acrylonitrile butadiene styrene, or ABS, is a common thermoplastic used to make light, rigid, molded products such as pipes, golf club heads. The styrene gives the plastic a shiny, impervious surface. The butadiene, a rubbery substance, provides resilience even at low temperatures. ABS can be used between −25 °C and 60 °C.

Mechanical Properties of ABS

Tensile Strength, Ultimate | 29.8 - 65 MPa | 4320 -9430 psi | Average = 41.5 MPa; Grade Count = 79
Tensile Strength, Yield | 29.6 - 65 MPa | 4290 -9430 psi | Average = 44.8 MPa; Grade Count = 143
Tensile Modulus | 1.79 - 3.2 GPa | 260 - 464 ksi | Average = 2.4 GPa; Grade Count = 141
Flexural Modulus | 1.606 -5.903 GPa | 233 - 856 ksi | Average = 2.4 GPa; Grade Count = 122
Flexural Yield Strength | 47.8 - 107 MPa | 6930 -15500 psi | Average = 71.8 MPa; Grade Count = 120

The outer case of the Robovac was originally designed to be .3 inches thick to support its outer walls. The weight of all the components inside of the Robovac will not exceed 15 lb. In order to correctly optimize the design a factor of safety of an additional 5 lb was added. To accurately simulate the load the design analysis was run with a distributed load of 20 lb over the bottom surface. The original analyze was run at a thickness of .3 inches however that was over designing hence adding to material cost. The analysis gave the group a max Von Mises stress of 1.0891e-1. The results can be seen in Figure 7 of Appendix.

The material that was chosen can withstand a lot more stress then applied. A Solidworks mass and volume optimization was performed to lessen the amount of material used. The team found that a wall thickness of .15 was acceptable thickness. The new analysis can
be seen in Figure 8 of Appendix.

The final design consists of a bridge for added support. The final bottom piece can be
seen in Figure 9 of Appendix.

Brush Optimization:

The brushes that will be used will be expected to rotate at 4500RPM . This transmitted centrifugal force will translate to a lot of stress on the rod. A finite element analysis was performed to measure its Von Mises stress and its max displacement. The max Von Mises stress on the assembly is 3 , which is reasonable because we are using .765psi ABS. It has a very high plastic deformation threshold. Below you will find the Von Mises stress and deformation analysis. Figure 10 in Appednix The brush configurations can be seen in Figure 11 in Appendix. The components consist of the infrared sensors Figure 12, the bumper Figure 13, the motor mount Figure 14, the microcontroller Figure 15, the battery Figure 16, the blower Figure 17, the display screen Figure 18 and the wireless transmitter Figure 19.

Battery

Objective:
The main focus of the battery part of the project is to provide enough power to all the components of the robot while lasting long enough to clean an average room without having to recharge. The battery should not add on excessive cost to the overall unit base price.

Customer Needs:
Based on customer research obtained through questionnaires and market research the following have been identified as the key focal points for the battery:

Clean room on a single charge Power numerous motors
Power sensors
Short recharge time
Full-charge current cutoff Minimize memory effect
Recharge docking station

Benchmark Data:
The following represents the battery specifications for current robotic vacuum cleaners on the market. In order to be able to compete successfully with the competition, the RoboVac must be able to at least meet and even exceed these specifications.

30 – 45 minutes run time
7 hour recharge time w/out rapid charger
3 hour recharge time w/ rapid charger (expensive option) 14.4 – 18 Volts
~ 3 Amp-hours
NiMH or NiCd chemistry
Recharge docking station

Selection Process:
In selecting a battery there are many factors that need to be taken into consideration assuring that all the needs are meant in a feasible manner. Most battery packs are comprised of individual battery cells connected in series but a connector tab.
Chemistry | Cost | Weight | Temp | Cycle Shelf Life Volts
| | | ( oC) | Life | (months) | per cell
Lead Acid | $$ | Very Heavy -65 to 80 300 | | | 12 | 2.0
Nickel Cadmium | $$ | Heavy | -20 to 65 500+ | | 6 | 1.2
Nickel Metal Hydride $$$ | | Moderate | -10 to 65 500 | | 12 | 1.2
Lithium Ion | $$$$ | Light | -20 to 60 500 | | 12 | 3.7
Lithium Polymer | $$$$$ Light | | -20 to 60 500 | | 12 | 3.7

The following lists the minimum requirements necessary for the battery to have in order to meet the needs of the RoboVac. The battery analysis is in Figure 20 of Appendix

- 18 volts
- 3000 milli-amp hour capacity
- max 12 in^2 area
- max $50 (not including charger)

Selected Battery:

Price: $ 23.95

Specifications:
Voltage (V) | 24
Capacity (mAh) | 5000
Cell Type | AA
Quantity | 20
Chemistry | NiMH
Short Time Discharging Rate (A) | 3.5
Continuous Usage Discharging Rate
(A) 1.8
Dimensions (in.) | 6x2x1.2
Weight (oz.) | 11

Selected Charger:

Price: $12.95

Specifications:
Voltage (V) | 24
Capacity (mA) | 500
Adaptor | DC
Connector | F-F

Motors

The system needs motors to power the rollers for cleaning and the wheels for motion. In the design, one motor is used to rotate the wheel base and one motor is used to rotate the wheels. The third motor is used to delivery power to the four brushes throughout the system. Compared to our competitors, we have decided to use one type of motor throughout the design. Since the system will be powered by a 24V battery, we decided to use the fastest spinning motor out of the researched.
Due to our design objectives to produce better suction power and a better cleaning effort all together, the team decided to chose one motor for the whole design to keep cost down while improving performance. The only downside to this decision is that it would make our design bigger, but since we are adding more volume (square vs. circle) we were able to keep the thickness to just less than 5 inches. The motors to be used ranged from 18-25mm in diameter.
After comparing the specs, it was decided that only one kind motor will go into the system. Choosing only one type will save money since it will be bought in bulk. The motor that was decided on was the Mabuchi RS-385SH-2270. The other one that was highly considered was the RS-380SH-4045, but that one needed a lot of current which did not help the longevity of the battery. The current output on the RS-380 Mabuchi motor is about 3.29 A. This is about three times more current than the highest in Roomba, which would reduce motor life.
Since we cannot fund money for R&D to test motors, it was decided to use the most powerful motor in the proven Roomba. The money for R&D that was spent by Roomba in testing the motors for durability and usability in their system is what we are basing our data on. These motors can be run at their max power since our system will have a battery which can provide the system with 24V of power, which is 10V more than Roomba.

Motor Specs
diameter (mm) | efficiency (%) | torque (mN*m) | current (A) | speed (rpm) | voltage (V)
RS-385SH-2270 | 25 | 66.3 | 9.56 | 1.06 | 14010 | 20
RS-360SH-10500 | 25 | 43.2 | 2.74 | 0.14 | 2590 | 12
FK-260SA-12300 | 17 | 60 | 1.96 | 0.2 | 7220 | 12
Series 2342-012 CR | 18 | 80 | 1 | 1.42 | 8100 | 12
Series 2342-018 CR | 18 | 81 | 0.99 | 1.01 | 8000 | 18
RS-380SH-4045 | 25 | 67.5 | 10.9 | 3.29 | 14060 | 7.2

Blowers (pressure drop in system)
As stated before, our main objective is to out clean the current market and improving suction is one way of accomplishing this. Improving suction power within the system can be done in many ways. The variables of which will let us know whether or not our fan achieved great suction are:

Power – speed of motor (rpm) plays a big role in how much suction is generated
Airway obstruction – dirty dustbins cause the performance in the vacuum to drop Orifice sizing – the intake ports (suction holes)
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

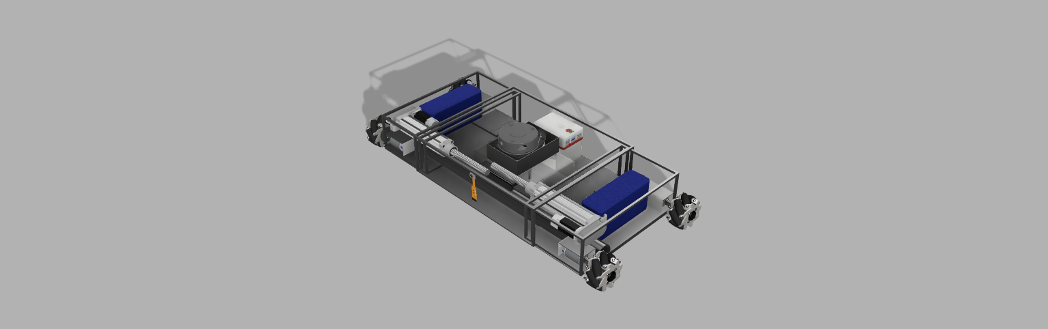
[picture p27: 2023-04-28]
Final Design v40.png

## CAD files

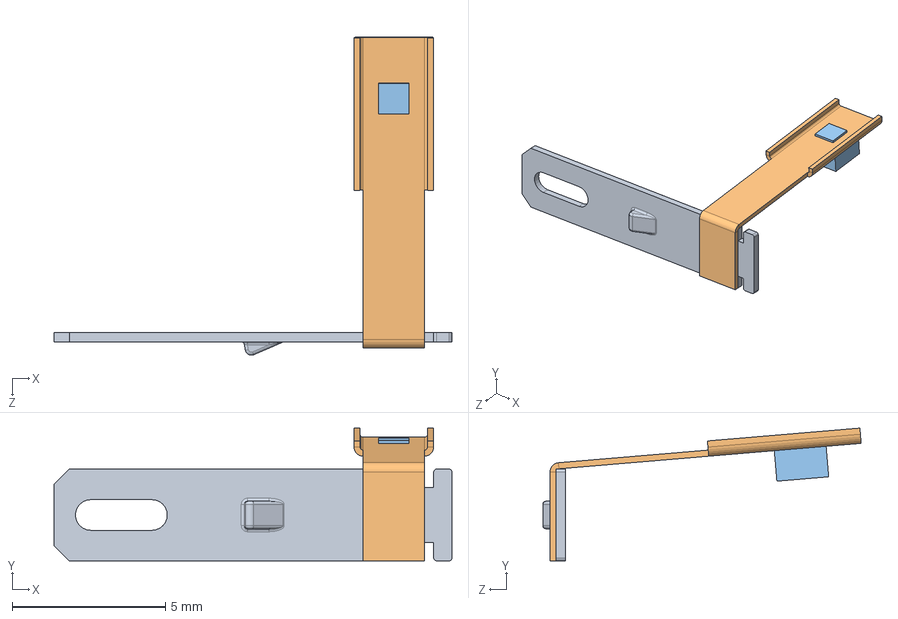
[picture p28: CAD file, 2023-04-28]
CAD/DC Motor/DC motor 8-12V/Contact^DC motor 8-12V.SLDASM
13.0 x 4.34 x 10.4 mm
Сonnector^DC motor 8-12V
Shaft contact^DC motor 8-12V
Graphite^DC motor 8-12V

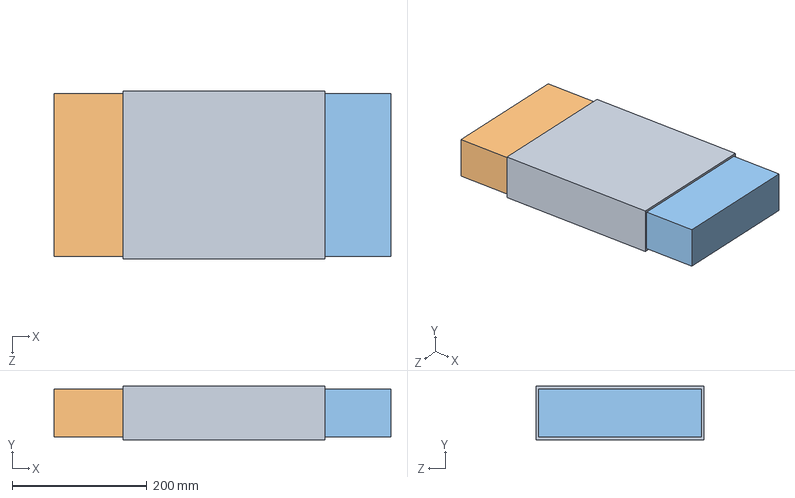
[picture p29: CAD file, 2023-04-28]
Simulation/Solidworks model/Assem.SLDASM
500.6 x 80.0 x 250.0 mm
Mid
Left
Right

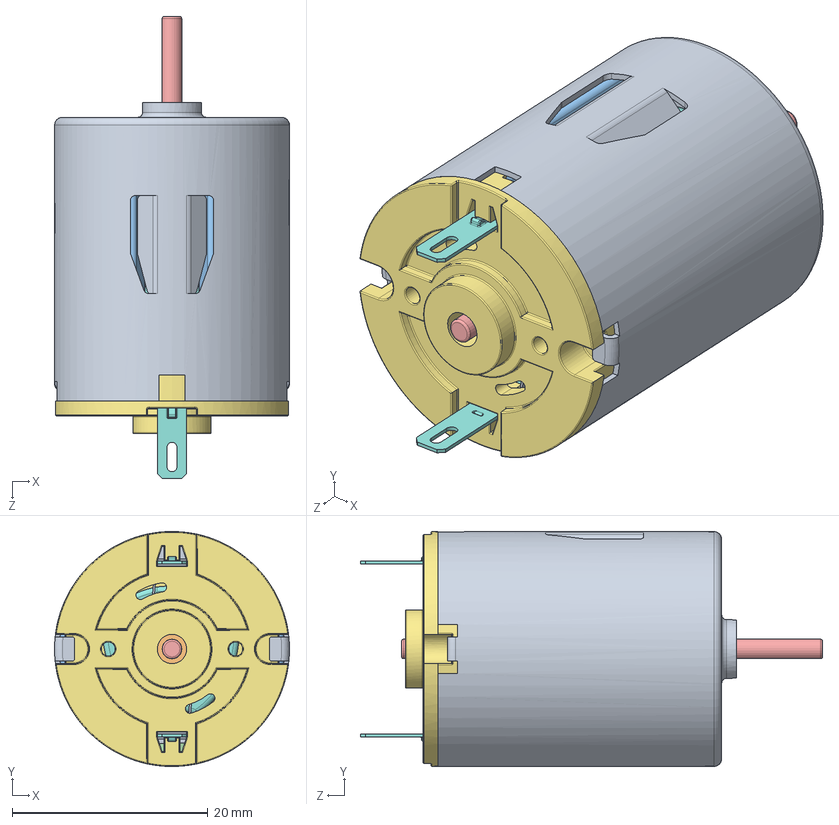
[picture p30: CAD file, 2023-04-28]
CAD/DC Motor/DC motor 8-12V/DC motor 8-12V.SLDASM
24.0 x 24.0 x 47.2 mm
Body^DC motor 8-12V
Plain bearing^DC motor 8-12V x 2
Magnet^DC motor 8-12V x 2
Spring^DC motor 8-12V
Shaft^DC motor 8-12V
Rotor plate^DC motor 8-12V x 26
Platinum Insulation^DC motor 8-12V x 2
Coil^DC motor 8-12V x 3
Insulating sleeve^DC motor 8-12V
Contact^DC motor 8-12V x 3
Spacer sleeve^DC motor 8-12V
Bushing for thrust^DC motor 8-12V x 2
Bushing^DC motor 8-12V
Sleeve for sliding^DC motor 8-12V
Cap^DC motor 8-12V
Сonnector^DC motor 8-12V x 2
Shaft contact^DC motor 8-12V x 2
Graphite^DC motor 8-12V x 2

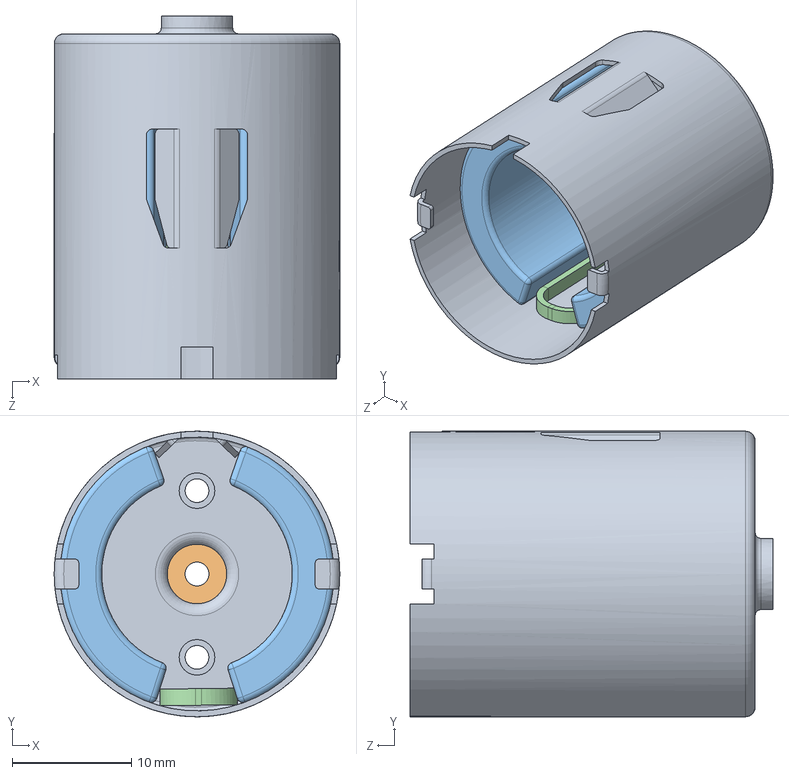
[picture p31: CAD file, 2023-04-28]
CAD/DC Motor/DC motor 8-12V/Body^DC motor 8-12V.SLDASM
24.0 x 24.0 x 30.5 mm
Body^DC motor 8-12V
Plain bearing^DC motor 8-12V
Magnet^DC motor 8-12V x 2
Spring^DC motor 8-12V

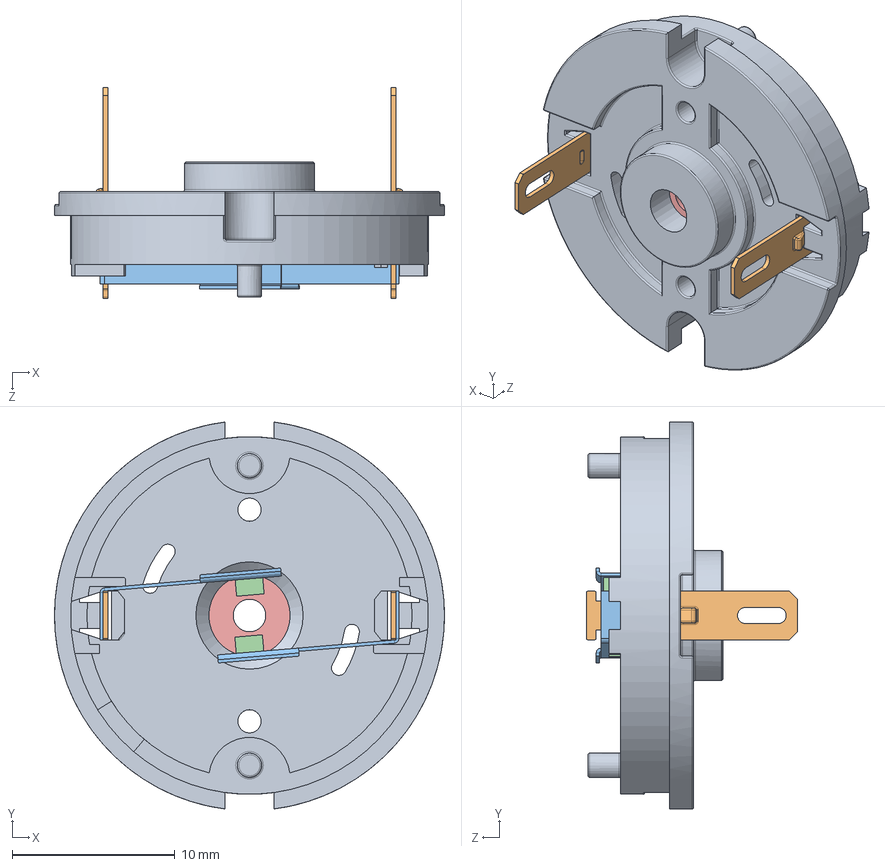
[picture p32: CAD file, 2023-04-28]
CAD/DC Motor/DC motor 8-12V/Cap^DC motor 8-12V.SLDASM
24.0 x 23.8 x 13.0 mm
Cap^DC motor 8-12V
Сonnector^DC motor 8-12V x 2
Shaft contact^DC motor 8-12V x 2
Graphite^DC motor 8-12V x 2
Plain bearing^DC motor 8-12V

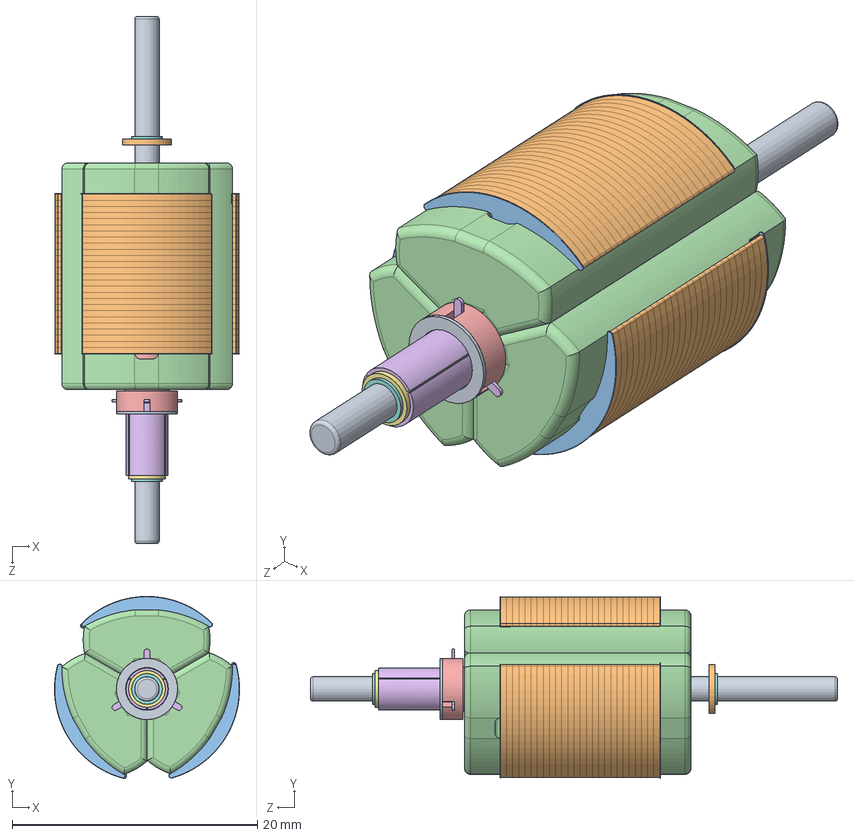
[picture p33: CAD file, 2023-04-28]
CAD/DC Motor/DC motor 8-12V/Shaft^DC motor 8-12V.SLDASM
15.1 x 14.9 x 43.0 mm
Shaft^DC motor 8-12V
Rotor plate^DC motor 8-12V x 26
Platinum Insulation^DC motor 8-12V x 2
Coil^DC motor 8-12V x 3
Insulating sleeve^DC motor 8-12V
Contact^DC motor 8-12V x 3
Spacer sleeve^DC motor 8-12V
Bushing for thrust^DC motor 8-12V x 2
Bushing^DC motor 8-12V
Sleeve for sliding^DC motor 8-12V

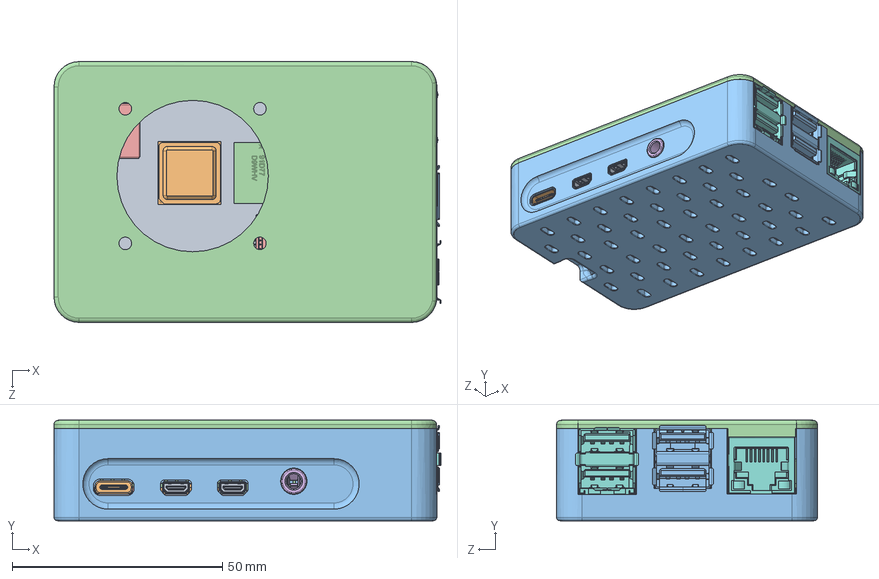
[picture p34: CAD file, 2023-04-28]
CAD/RP/raspberry pi 4 model b enclosure/Raspberry Pi 4 Model B.SLDASM
92.0 x 23.9 x 62.0 mm
PCB, RPi4ModelB
Broadcom BCM2711B0 CPU, RPi4ModelB
2.54 mm DUPONT MALE PIN HEADER, POE, 2X2, RPi4ModelB
2.54 mm DUPONT MALE PIN HEADER, IO, 2X20, RPi4ModelB
Camera Connector, RPi4ModelB
Microphone Plug, RPi4ModelB
Display Connector, RPi4ModelB
Gigabit Ethernet Port, RPi4ModelB
Female Micro HDMI Connector, RPi4ModelB x 2
Female USB Type C Connector, RPi4ModelB
2X USB3.0 PORTS, RPi4ModelB
91D77 D9WHV 778K, 4 GB LPDDR4 SDRAM, RPi4ModelB
Cypress CYW43455 Wireless Module Cover, RPi4ModelB
SD Card Slot, RPi4ModelB
VIA VL805 PCIe USB 3.0 controller, RPi4ModelB
2X USB2.0 PORTS, RPi4ModelB
Broadcom BCM54213PE Gigabit Ethernet Transceiver, RPi4ModelB
MxL7704 Universal PMIC, RPi4ModelB
Bottom
Top

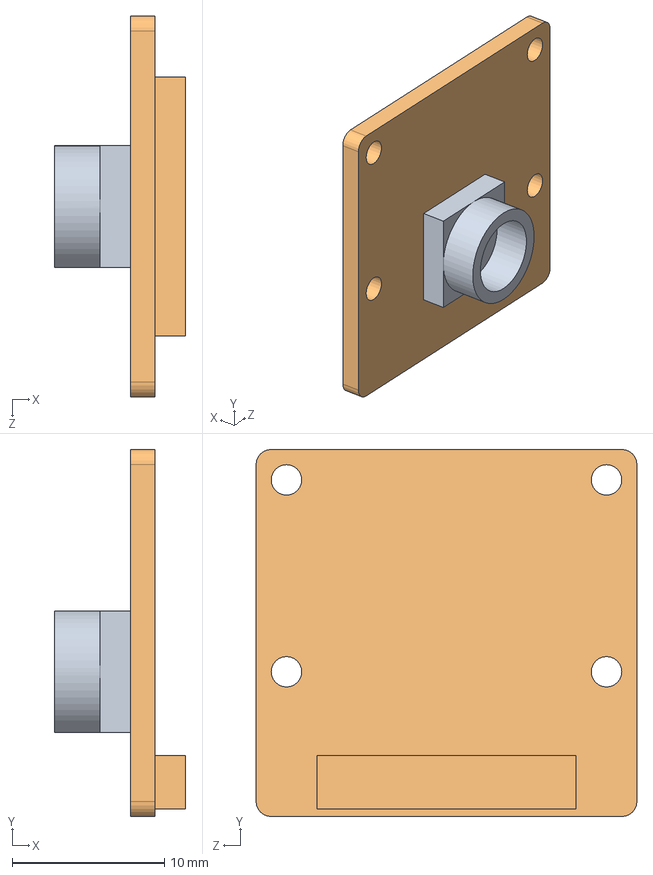
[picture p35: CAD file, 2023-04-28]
CAD/Raspberry Pi/Raspberry Pi 4_/Camera Module V2. .SLDPRT.SLDASM
8.60 x 24.1 x 25.0 mm
Camera
Camera PCB

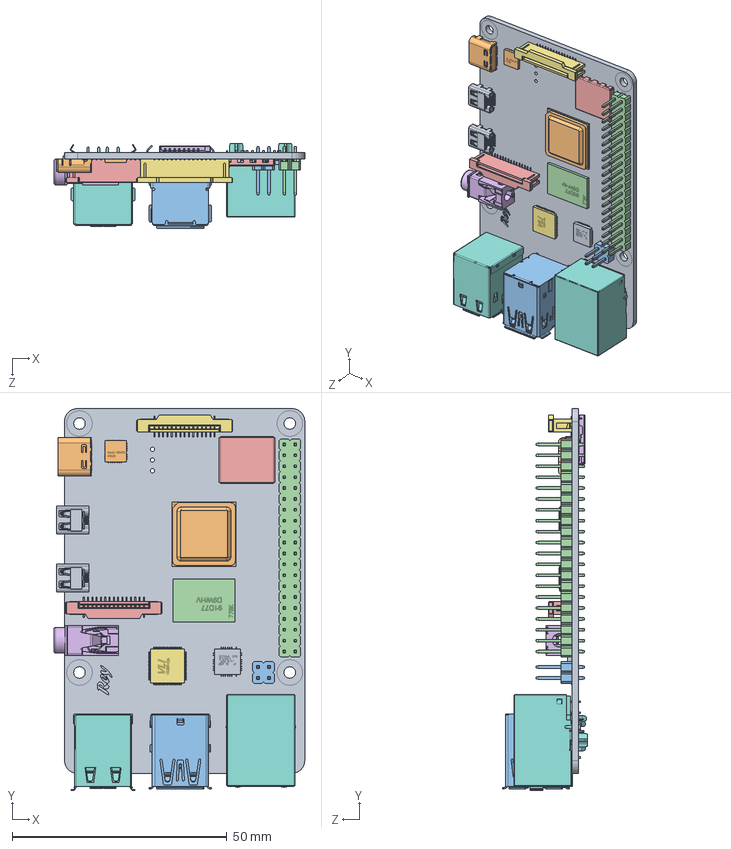
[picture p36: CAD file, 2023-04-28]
CAD/Raspberry Pi/Raspberry Pi 4_/Raspberry Pi 4.SLDASM
58.4 x 89.0 x 19.9 mm
PCB, RPi4ModelB
Broadcom BCM2711B0 CPU, RPi4ModelB
2.54 mm DUPONT MALE PIN HEADER, POE, 2X2, RPi4ModelB
2.54 mm DUPONT MALE PIN HEADER, IO, 2X20, RPi4ModelB
Camera Connector, RPi4ModelB
Microphone Plug, RPi4ModelB
Display Connector, RPi4ModelB
Gigabit Ethernet Port, RPi4ModelB
Female Micro HDMI Connector, RPi4ModelB x 2
Female USB Type C Connector, RPi4ModelB
2X USB3.0 PORTS, RPi4ModelB
91D77 D9WHV 778K, 4 GB LPDDR4 SDRAM, RPi4ModelB
Cypress CYW43455 Wireless Module Cover, RPi4ModelB
SD Card Slot, RPi4ModelB
VIA VL805 PCIe USB 3.0 controller, RPi4ModelB
2X USB2.0 PORTS, RPi4ModelB
Broadcom BCM54213PE Gigabit Ethernet Transceiver, RPi4ModelB
MxL7704 Universal PMIC, RPi4ModelB

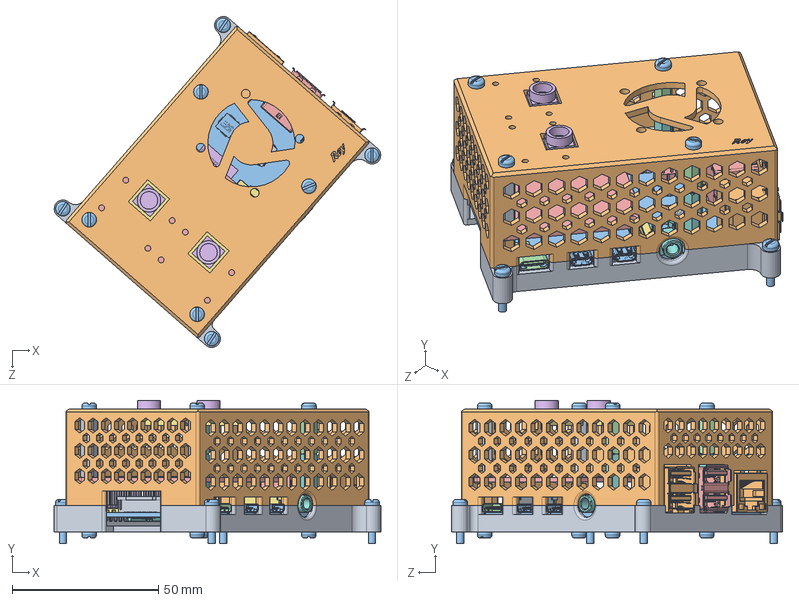
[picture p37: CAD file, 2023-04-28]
CAD/Raspberry Pi/Raspberry Pi 4_/Raspp Pi 4.SLDASM
111.6 x 49.0 x 113.1 mm
Pi 4 Case Bottom
Pi 4 Case Top
PCB, RPi4ModelB
Broadcom BCM2711B0 CPU, RPi4ModelB
2.54 mm DUPONT MALE PIN HEADER, POE, 2X2, RPi4ModelB
2.54 mm DUPONT MALE PIN HEADER, IO, 2X20, RPi4ModelB
Camera Connector, RPi4ModelB
Microphone Plug, RPi4ModelB
Display Connector, RPi4ModelB
Gigabit Ethernet Port, RPi4ModelB
Female Micro HDMI Connector, RPi4ModelB x 2
Female USB Type C Connector, RPi4ModelB
2X USB3.0 PORTS, RPi4ModelB
91D77 D9WHV 778K, 4 GB LPDDR4 SDRAM, RPi4ModelB
Cypress CYW43455 Wireless Module Cover, RPi4ModelB
SD Card Slot, RPi4ModelB
VIA VL805 PCIe USB 3.0 controller, RPi4ModelB
2X USB2.0 PORTS, RPi4ModelB
Broadcom BCM54213PE Gigabit Ethernet Transceiver, RPi4ModelB
MxL7704 Universal PMIC, RPi4ModelB
Arducam Multi Camera Adapter Module V2.2
Camera x 2
Camera PCB x 2
M2.5 Standoff Female-Female x 2
M2.5 Standoff Male-Female 21mm x 2
M2.5 Standoff Female-Female 10mm x 2
pan slot head_am x 12
M2.5 Standoff Male-Female 13mm x 2

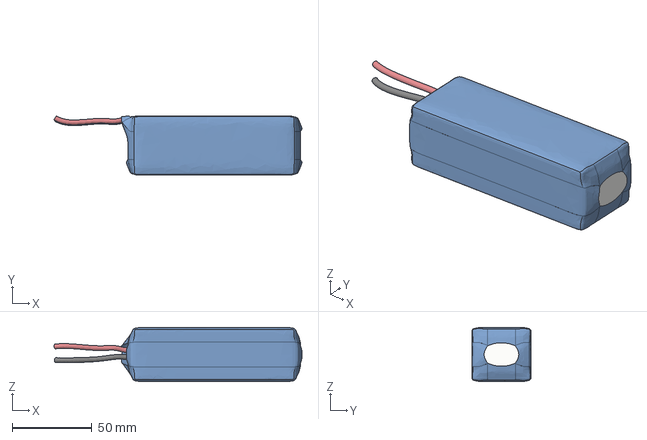
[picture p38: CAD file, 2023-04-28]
CAD/2200 mAh Battery/Turnigy nano-tech 2200mah 4S 25~50C Lipo Pack v13.iges
155.3 x 37.1 x 34.0 mm

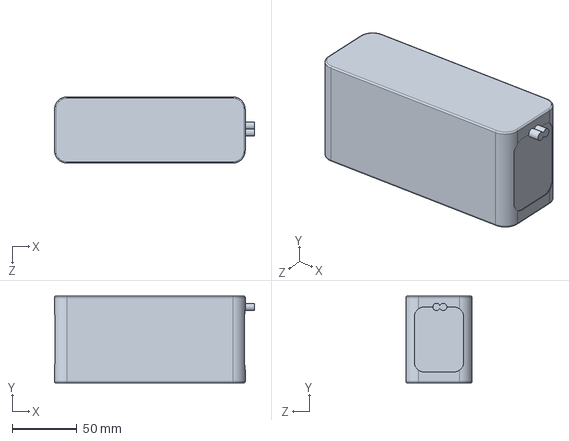
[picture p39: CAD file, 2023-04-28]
CAD/5000 mAh Battery/Lipo Battery-5000mAh 7S 60C-Turnigy.SLDPRT
154.1 x 67.0 x 51.0 mm

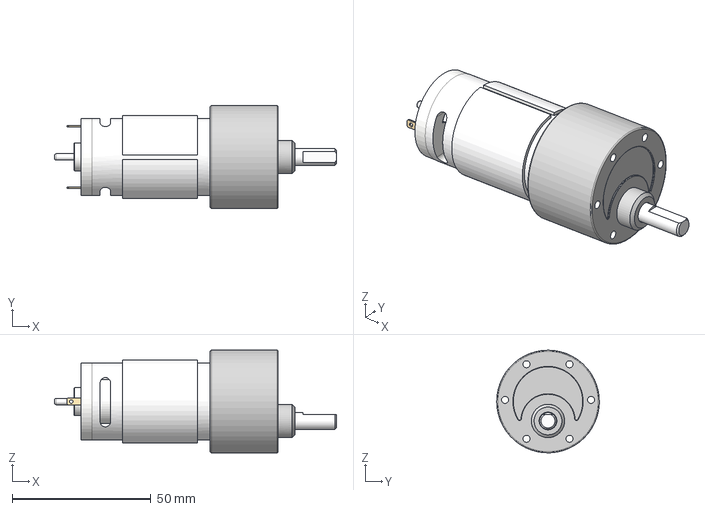
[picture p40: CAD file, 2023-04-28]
CAD/DC Motor Large/DC Motor 8347631 v3.step
101.6 x 37.0 x 37.0 mm

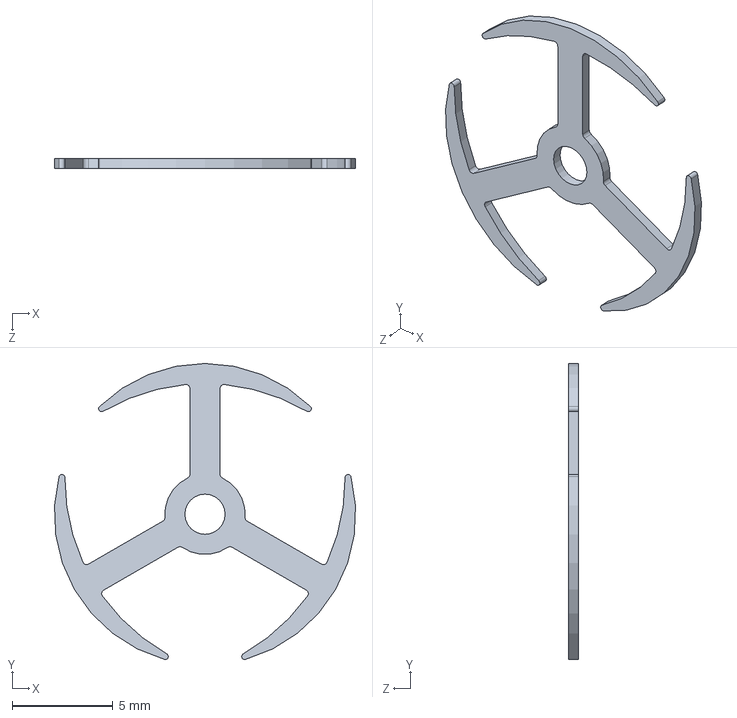
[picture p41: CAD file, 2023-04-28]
CAD/DC Motor/DC motor 8-12V/Rotor plate^DC motor 8-12V.SLDPRT
15.0 x 14.7 x 0.5 mm

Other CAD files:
CAD/Raspberry Pi/Raspberry Pi 4_/Raspberry Pi 4 Model B.SLDASM
CAD/Pi Camera Module/ov5647af_rpi_camera.STEP
CAD/Pi Camera Support/Raspberry Pi Camera support/SupCamera_SwivelJoint.step
CAD/Raspberry Pi/Raspberry Pi 4_/2.54 mm DUPONT MALE PIN HEADER, IO, 2X20, RPi4ModelB.SLDPRT
CAD/2200 mAh Battery/Turnigy nano-tech 2200mah 4S 25~50C Lipo Pack.step
CAD/DC Motor/DC motor 8-12V/Body^DC motor 8-12V.SLDPRT
CAD/DC Motor/DC motor 8-12V/Bushing for thrust^DC motor 8-12V.SLDPRT
CAD/DC Motor/DC motor 8-12V/Bushing^DC motor 8-12V.SLDPRT
CAD/DC Motor/DC motor 8-12V/Cap^DC motor 8-12V.SLDPRT
CAD/DC Motor/DC motor 8-12V/Coil^DC motor 8-12V.SLDPRT
CAD/DC Motor/DC motor 8-12V/Contact^DC motor 8-12V.SLDPRT
CAD/DC Motor/DC motor 8-12V/DC motor 8-12V.SLDPRT
CAD/DC Motor/DC motor 8-12V/DC motor 8-12V_.IGS
CAD/DC Motor/DC motor 8-12V/Graphite^DC motor 8-12V.SLDPRT
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

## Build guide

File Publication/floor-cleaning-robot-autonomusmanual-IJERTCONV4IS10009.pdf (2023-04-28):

# Floor Cleaning Robot (Autonomus/Manual)

Vatsal N Shah
EC Department
Indus University, Ahmedabad, India

Sathvik K P V S
EC Department
Indus University, Ahmedabad, India

Asst. Prof. Abhishek Vaghela EC Department
Indus University, Ahmedabad, India

Abstract—Households of today are becoming smarter and more automated. Home automation delivers convenience and creates more time for people. Domestic robots are entering the homes and people’s daily lives, but it is yet a relatively new and immature market. However, a growth is predicted and the adoption of domestic robots is evolving. Several robotic vacuum cleaners are available on the market but only few ones implement wet cleaning of floors. The purpose of this paper is to design and implement a Vacuum Robot Autonomous and Manual via Phone Application. Vacuum Cleaner Robot is designed to make cleaning process become easier rather than by using manual vacuum. To design and implement a vacuum robot prototype by using Arduino Mega, Arduino Shield, LDR Sensor, Real Time Clock, Motor Shield L293D, Ultrasonic Sensor, and IR Sensor to achieve the goal. Vacuum Robot will have several criteria that are user-friendly.Consequently, a prototype robot has been manufactured and tested in the laboratory.

Keywords—Vaccum cleaner; RTC; Bluetooth; IR sensor; Arduino; Ultrasonic sensor

I. INTRODUCTION

The research and development of an autonomous mobile robot and a Manual Phone Application Control prototype able to vacuum cleaning a room or even an entire house is not a trivial challenge. In order to tackle such a task, so that it could be completed in six weeks (the duration of the course), some simplifications and assumptions were made to the designers initial idea of an “ideal” autonomous/manual vacuum cleaner. In this way, some functional requirements that would improve the robot performance were not taking into account due either to their inherent complexity or to their mechanical implications. These robots operate semi- or fully autonomously to perform services useful to the well-being of humans and equipment. With the aim of keeping our robot as simple as possible, while able to perform the initial goals, i.e. an autonomous vacuum cleaner robot able to randomly navigate through a room or a house with the minimum human assistance, the following specifications were found:
- Obstacle avoidance
- Floor detection
- Collision detection
- Fan motor monitoring
- Light Sensing
- Real Time Clock
- System on automatically
These specifications correspond to some of the expected behaviors that will be programmed into the robot. Other behaviors that will increase the overall performance of the robot.

In this section i.e. In Section 2 we will discuss about the background details about the project which includes about the android platform, connectivity, dc motor, l298D motor shield and Arduino Mega board, Sensors, Vacuum Mechanism, Display, Real Time clock. In Section 3 we will discuss about the Application Software part and in Section 4 result and analysis.

II. DESIGN METHODOLOGY

A number of software and hardware implementation techniques were used to design and develop the system. Fig. 1 shows the block diagram of system. We used a 12VDC motor, L293D IC, Different Sensors, Real Time Clock, Vacuum mechanism and Arduino to develop our system.

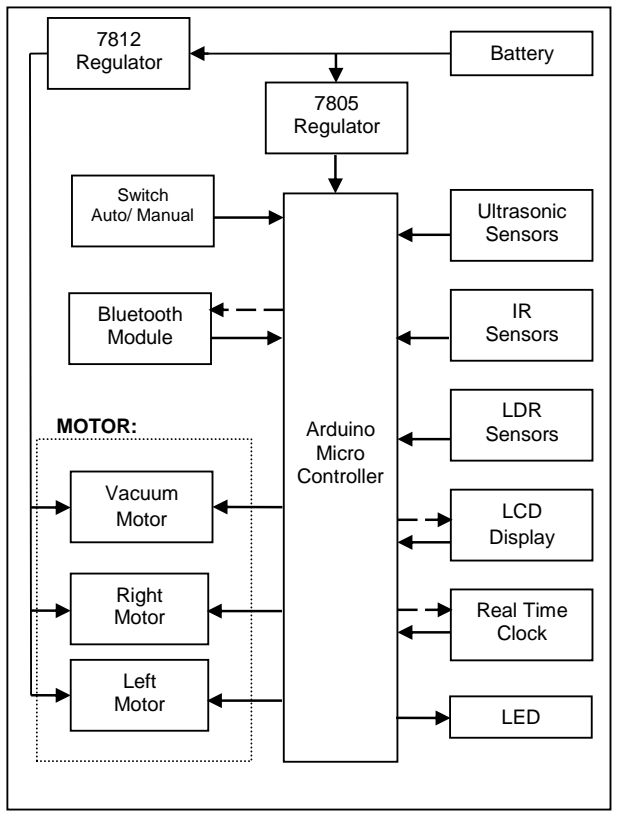
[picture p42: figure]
Switch Auto/ Manual; Bluetooth Module; Ultrasonic Sensors; IR Sensors; LDR Sensors; Left Motor; Right Motor; MOTOR:; Arduino; Micro Controller; LCD Display; Real Time Clock; Vacuum Motor; Battery; 7805 Regulator; 7812 Regulator; LED

Fig. 1. Block Diagram of system

The operation of the robotic vacuum is going to be based on retrieving data from an array of inputs that will tell the condition of the floor space around the vacuum. These inputs

International Journal of Engineering Research & Technology (IJERT) ISSN: 2278-0181

Published by, www.ijert.org

NCIMACEMT - 2016 Conference Proceedings

Volume 4, Issue 10

Special Issue - 2016 include sonar, LDR sensor, and IR sensor. Each of these parts will be described in further detail further on later in the documentation. The data from these inputs will be fed into the chip(s) which through its software program will decide which direction the vacuum should move by sending the control signals out to the drive motors.

Components:

A. Microcontroller: Arduino Mega 2560
The Arduino Mega is a microcontroller board based on the ATmega1280 (datasheet). It has 54 digital input/output pins (of which 14 can be used as PWM outputs), 16 analog inputs, 4 UARTs (hardware serial ports), a 16 MHz crystal oscillator, a USB connection, a power jack, an ICSP header, and a reset button. It contains everything needed to support the microcontroller; simply connect it to a computer with a USB cable or power it with AC-to-DC adapter or battery to get started.

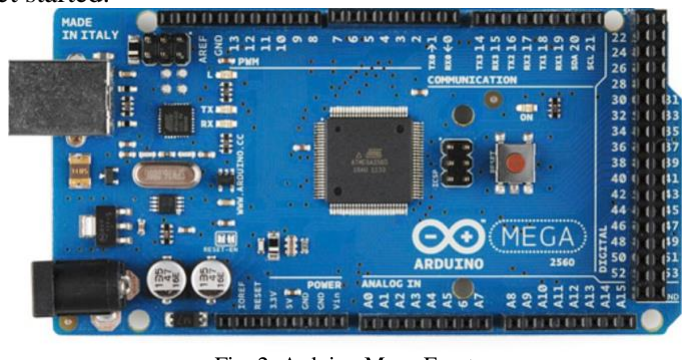
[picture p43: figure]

Fig. 2. Arduino Mega Front
B. DC Motor
Almost every mechanical movement that we see around us is accomplished by an electric motor. Electric machines are means of converting conventional energy. Motors take electrical energy and produce mechanical energy. Electric motor is used to power hundreds of devices we use in everyday life. An example of motor used in day to day life is automobiles, food blenders and so is vacuum cleaner.
C. Bluetooth (HC-06)
For the communication of the robot with the cell phone or a mobile we are using the Bluetooth device. The Bluetooth device (HC-06) is attached to the robot that receives the data from the mobile and also it can transmit the data. It is used for converting serial port to Bluetooth. It has two modes: Master and Slave. Bluetooth is a wireless communication protocol running at the speed of 2.4 GHz with the architecture of client-server and which is suitable for forming personal area networks. It is designed for devices such as mobile phones (low power). Bluetooth protocol uses the MAC address of the device. Bluetooth gives the connectivity between two devices using their MAC address.

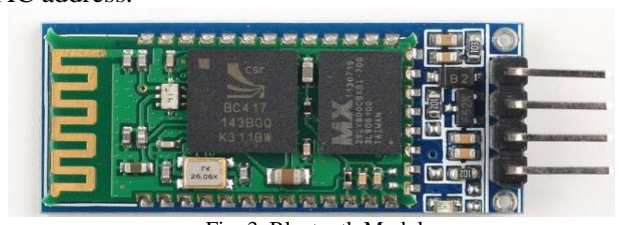
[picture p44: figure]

Fig. 3. Bluetooth Module

D. IR Sensor
The sensor consists of two eyes. One eye sends the infrared light and the other eye sees the reflection of that infrared light and measures the distance which is then sent to the Arduino through analog input to perform further operations based on the distance. There are three wires coming from the sensor .i.e. Red, Black and White or it can be Red, Brown and Yellow. Red is connected to 5V of Arduino. Black or brown to Ground of Arduino. White or yellow to analog input pin of Arduino i.e. in this case to analog pin 0.

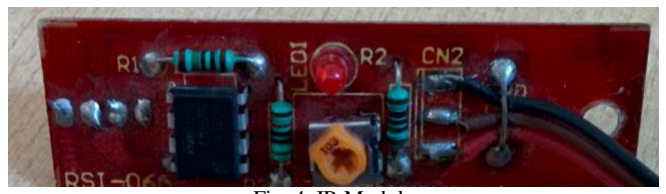
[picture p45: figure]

Fig. 4. IR Module
E. LDR Sensor
The light dependent resistor is an electronic component whose resistance decreases with increasing light intensity. It is also called as “Photo Resistor” or “Photo conductor”. The light dependent resistor uses high resistance semiconductor material. When light falls on such a semiconductor the bound electrons [i.e., Valence electrons] get the light energy from the incident photos. Due to this additional energy, these electrons become free and jump in to the conduction band. The electron –hole pairs are generated. Due to these charge carriers, the conductivity of the device increases, decreasing its resistivity.

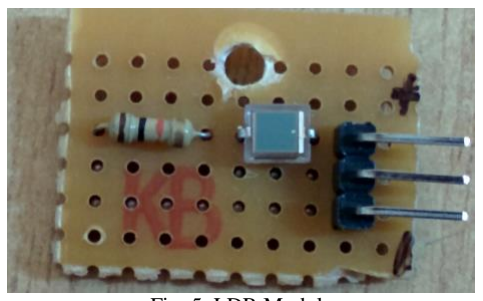
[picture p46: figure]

Fig. 5. LDR Module
F. Ultrasonic Sensor
This sensor is a high performance ultrasonic range finder. It is compact and measures an amazingly wide range from 2cm to 4m. This ranger is a perfect for any robotic application, or any other projects requiring accurate ranging information. This sensor can be connected directly to the digital I/O lines of your microcontroller and distance can be measured in time required for travelling of sound signal using simple formula as below. Distance = (Echo pulse width high time * Sound Velocity (340M/S)/2) or Distance in cm = (Echo pulse width high time (in us)*0.017) The module works on 5VDC input and also gives an output signal directly for detection of any obstacle up to 4M.Power up the sensor by 5VDC using pins “VCC” and “GND”. First of all a 10us trigger input has to be given to the pin named “Trig” on the sensor. This starts one cycle of range conversion and sends 8 bursts of sound waves from the transmitter. As soon as the signals are transmitted the

“Echo” pin goes to high level and remains in high level until the same sound waves are received by the receiver. If the received sound waves are same as what the same sensor transmitted then the Echo pin goes to low level. If no object is detected within 5M after 30ms the Echo signal will automatically go to low level.

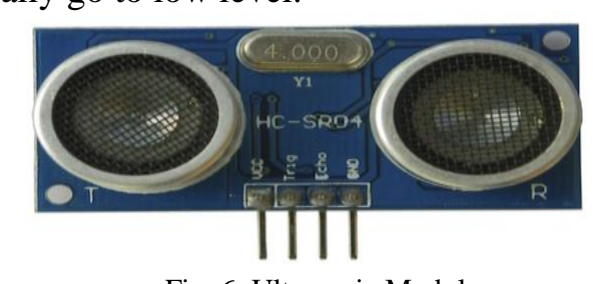
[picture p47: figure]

Fig. 6. Ultrasonic Module
G. Real Time Clock
A real-time clock (RTC) is a computer clock (most often in the form of an integrated circuit) that keeps track of the current time. Although the term often refers to the devices in personal computers, servers and embedded systems, RTCs are present in almost any electronic device which needs to keep accurate time.
Although keeping time can be done without an RTC, using one has benefits:
1. Low power consumption (important when running from alternate power)
2. Frees the main system for time-critical tasks
3. Sometimes more accurate than other methods

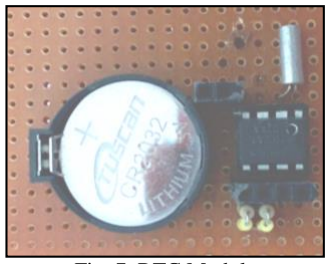
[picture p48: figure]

Fig. 7. RTC Module
H. LCD Module
A liquid crystal display (LCD) is a flat panel display, electronic visual display, or video display that uses the light modulating properties of liquid crystals. Liquid crystals do not emit light directly. 20x4 means that 20 characters can be displayed in each of the 4 rows of the 20x4 LCD, thus a total of 80 characters can be displayed at any instance of time.

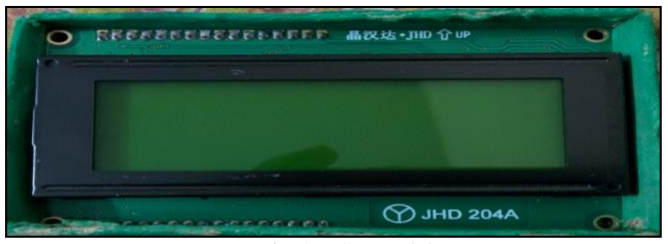
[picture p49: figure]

Fig. 8. LCD Module

III. APPLICATION SOFTWARE

The Android app is generally developed using JAVA language. The app controlling this vacuum robot can be built without having the knowledge in java language. It is called as “VBot211” developed by MIT App Inventor. Shown below is a diagram which shows the interface of the app. The app shown below has 5 buttons and all the button gives 5 different bytes in the output that is to be fed to the microcontroller to further process. For e.g. if we press Up! Button, the Bluetooth module will give 1 byte at its output.

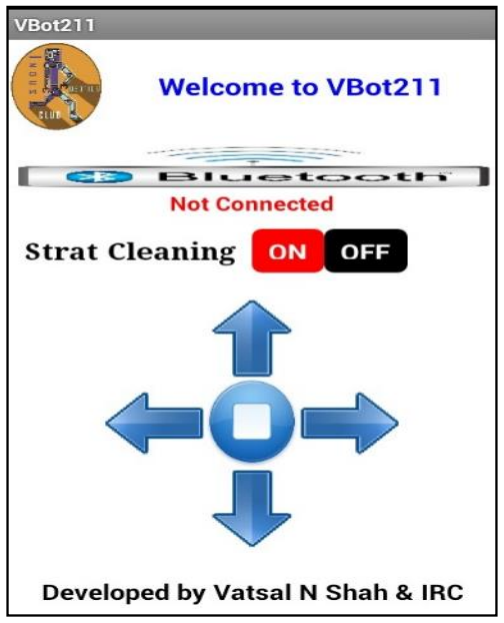
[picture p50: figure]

Fig. 9. Application Display

The app invented by these searches for the Bluetooth devices along with their MAC addresses. The user just needs to select a particular MAC Address. When a particular MAC is selected, the status shown on the screen is “Connected”.

IV. RESULT AND ANALYSIS
Firstly, when we switch on the robot, it initializes for few seconds as shown in the fig. 10 and then, it asks for which mode we want to select i.e. automatic or manual. For automatic mode press Switch “ON” and for manual mode press Switch “OFF” as shown from fig. 11 onwards.

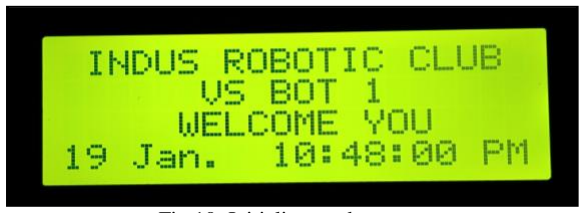
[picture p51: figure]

Fig 10: Initializes and start-up

Fig. 11 shows Automatic mode is selected by pressing switch, and no obstacle is detected by IR sensor and distance of Ultrasonic sensor is also less than 11cm so move FORWARD. And intensity of light is more by LDR sensor i.e., greater than 150, so LEDs OFF.

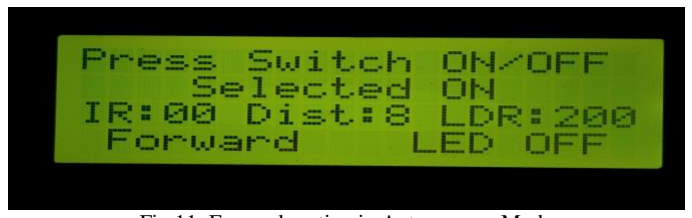
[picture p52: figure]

Fig 11: Forward motion in Autonomous Mode

Fig. 12 shows Automatic mode is selected by pressing switch, and obstacle is detected at left side by IR sensor and distance of Ultrasonic sensor is also less than 11cm so move RIGHT. And intensity of light is more by LDR sensor i.e., greater than 150, so LEDs OFF.

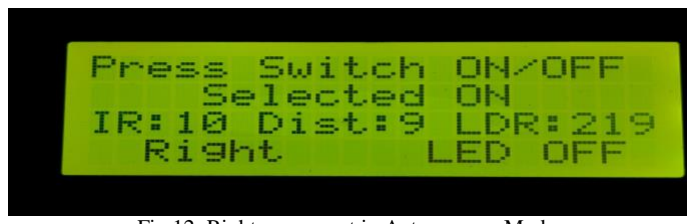
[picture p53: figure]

Fig 12: Right movement in Autonomous Mode

Fig. 13 shows Automatic mode is selected by pressing switch, and obstacle is detected at right side by IR sensor and distance of Ultrasonic sensor is also less than 11cm so move LEFT. And intensity of light is more by LDR sensor i.e., greater than 150, so LEDs OFF.

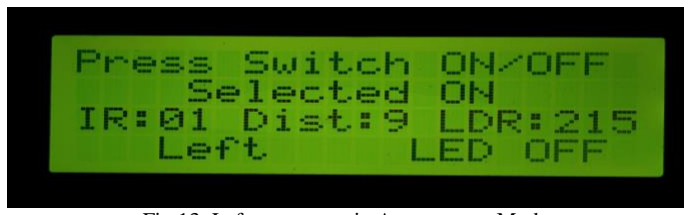
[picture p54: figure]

Fig 13: Left movement in Autonomous Mode

Fig. 14 shows Automatic mode is selected by pressing switch, and obstacle is detected at both sides by IR sensor and distance of Ultrasonic sensor is also less than 11cm so STOP and move BACKWARD. And intensity of light is more by LDR sensor i.e., greater than 150, so LEDs OFF.

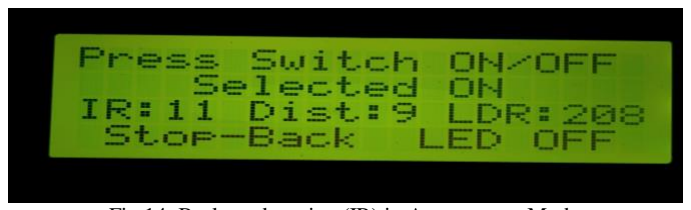
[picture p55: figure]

Fig 14: Backward motion (IR) in Autonomous Mode

Fig. 15 shows Automatic mode is selected by pressing switch, and no obstacle is detected by IR sensor but distance of Ultrasonic sensor is more than equal to 11cm so STOP and move BACKWARD. And intensity of light is more by LDR sensor i.e., greater than 150, so LEDs OFF.

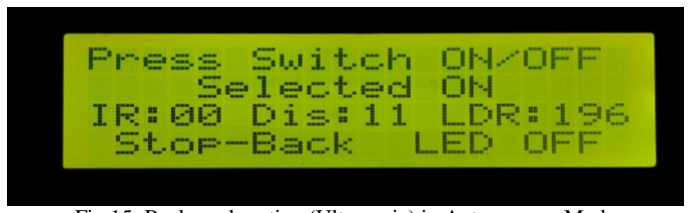
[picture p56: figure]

Fig 15: Backward motion (Ultrasonic) in Autonomous Mode

Fig. 16 shows Manual mode is selected by not pressing switch, and Bluetooth is connected and received FORWARD motion. And intensity of light is more by LDR sensor i.e., greater than 150, so LEDs OFF.

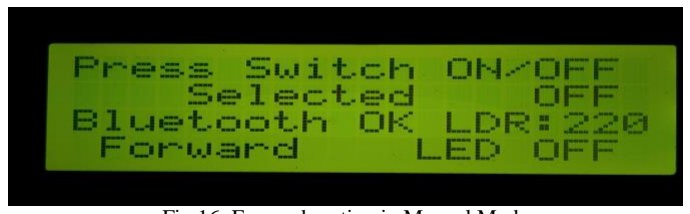
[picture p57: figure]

Fig 16: Forward motion in Manual Mode

Fig. 17 shows Manual mode is selected by not pressing switch, and Bluetooth is connected and received LEFT motion. And intensity of light is more by LDR sensor i.e., greater than 150, so LEDs OFF.

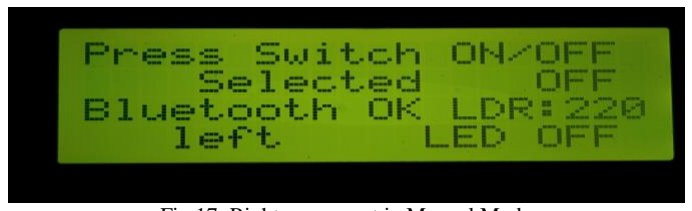
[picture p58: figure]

Fig 17: Right movement in Manual Mode

Fig. 18 shows Manual mode is selected by not pressing switch, and Bluetooth is connected and received RIGHT motion. And intensity of light is more by LDR sensor i.e., greater than 150, so LEDs OFF.

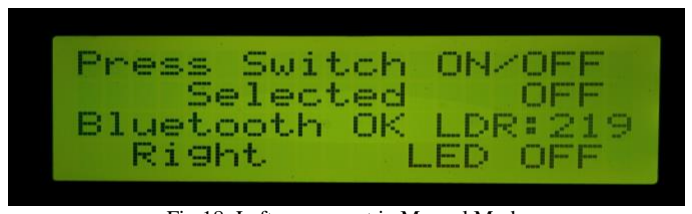
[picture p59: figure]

Fig 18: Left movement in Manual Mode

Fig. 19 shows Manual mode is selected by not pressing
switch, | and | Bluetooth | is | connected | and | received
BACKWARD motion. And intensity of light is more by LDR sensor i.e., greater than 150, so LEDs OFF.

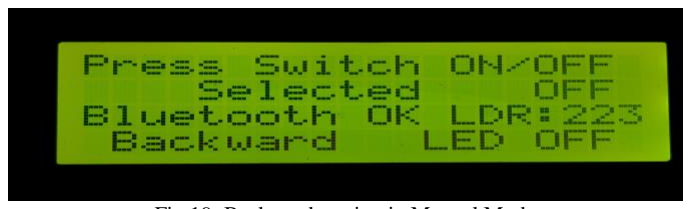
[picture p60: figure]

Fig 19: Backward motion in Manual Mode

Fig. 20 shows Manual mode is selected by not pressing switch, and Bluetooth is connected and received VACUUM ON. And intensity of light is more by LDR sensor i.e., greater than 150, so LEDs OFF.

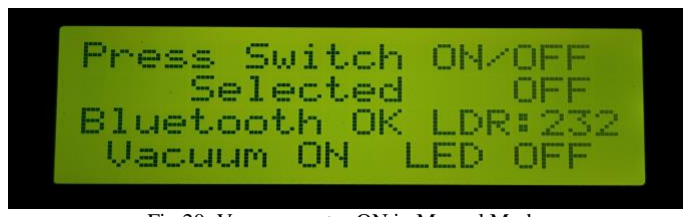
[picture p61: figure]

Fig 20: Vacuum motor ON in Manual Mode

Fig. 21 shows Manual mode is selected by not pressing switch, and Bluetooth is connected and received VACUUM OFF. And intensity of light is more by LDR sensor i.e., greater than 150, so LEDs OFF.

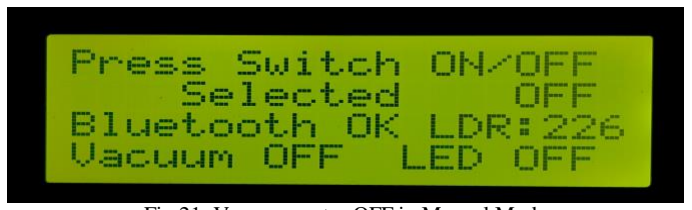
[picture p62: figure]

Fig 21: Vacuum motor OFF in Manual Mode

Fig. 22 shows Manual mode is selected by not pressing switch, and Bluetooth is not connected so STOP. And intensity of light is more by LDR sensor i.e., greater than 150, so LEDs OFF.

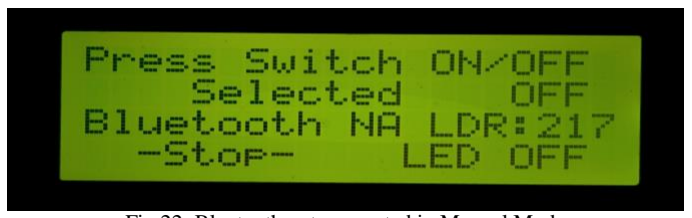
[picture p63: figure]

Fig 22: Bluetooth not connected in Manual Mode

Fig. 23 intensity of light is less by LDR sensor i.e., less than 150, so LEDs ON.

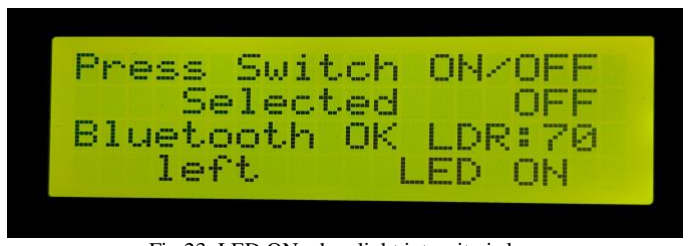
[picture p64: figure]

Fig 23: LED ON when light intensity is low

The operation of different components in Autonomous and Manual mode is shown below.

TABLE I. | OPERATION OF COMPONENETS IN DIFFERENT MODES
Components↓ Modes→ | Autonomous mode | Manual mode
LCD | ✓ | ✓
RTC | ✓ | ✓
LDR | ✓ | ✓
LED | ✓ | ✓
Switch | ✓ | ✓
Base Motors | ✓ | ✓
Vacuum Motor | ✓ | ✓
IR Sensors | ✓ | NA
Ultrasonic | ✓ | NA
Bluetooth | NA | ✓
V. CONCLUSION

This research facilitates efficient floor cleaning with sweeping operations. This robot works in two modes automatic and manual for user convenience. This proposed work provides the hurdle detection in case of any obstacle that comes in its way. The obstacle detection range is 1ft. Bluetooth modules provide wireless communication between remote and robot and their range is 10m. If there is hurdle in the way of robot, it sends the information to the remote which gets displayed on the LCD. User can also operate this robot manually with the help of remote. It reduces the labor cost and saves time also and provides efficient cleaning. In automatic mode, the robot operates autonomously. The operations such as sweeping and changing the path in case of hurdle are performed automatically.
Nonetheless, there are still new ideas to improve the developed system and to add new functionality to it. Instead of Bluetooth module RF module and XBee pro series module can be used to improve the range of wireless communication. GSM module can be used to send message that, the robot has done the cleaning task. Camera can be used for navigation purposes. Vacuum cleaning can also be done with sweeping and mopping. Further, the robot can be made to move randomly in any direction and its speed can be controlled. Battery monitoring, self-charging, lighter body weight and to set alarm on/off time manually can be improved.

REFERENCES

[1] S.Muruganandhan, G.Jayabaskaran, P.Bharathi, “LabVIEW-NI ELVIS II based Speed Control of DC Motor,” International Journal of Engineering Trends and Technology (IJETT) Volume 4 Issue 4, April 2013
[2] Liu, Kuotsan, Wang, Chulun, “A Technical Analysis of Autonomous Floor Cleaning Robots Based on US Granted Patents”, European International Journal of Science and Technology Vol. 2 No. 7, September 2013.
[3] Ashish chaple, Sujata Bhaskarwar, Ashay Bhaskarwar, Sadhana Chidarwar, “Autonomous Cleaning Robot”, MPGI National Multi Conference 2012 (MPGINMC-2012) April, 2012
[4] Aiman Ansari, Yakub Ansari, Saquib Gadkari, Aarti Gokul, “Android App Based Robot”, (IJCSIT) International Journal of Computer Science and Information Technologies, Vol. 6 (2) , June 2015
[5] Abhishek Pandey , Anirudh Kaushik, Amit Kumar Jha, Girish Kapse, “A Technological Survey on Autonomous Home Cleaning Robots”, International Journal of Scientific and Research Publications, Volume 4, Issue 4, April 2014
[6] Manreet Kaur, Preeti Abrol, “Design and Development of Floor Cleaner Robot (Automatic and Manual)”, International Journal of Computer Applications Volume 97– No.19, July 2014
[7] Mr. S. Deepak, Mr. I. Ambrose Edward, “Automatic Floor Cleaner (The Wireless Wiper)” International Journal of Engineering Research & Technology (IJERT) Vol. 3 Issue 2, February - 2014
[8] HC-06 Bluetooth Module, http://www.Lanwind.com/files/hc-06en.pdf.

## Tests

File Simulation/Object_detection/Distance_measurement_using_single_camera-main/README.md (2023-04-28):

# Distance measurement using single:one:camera :camera:

  

If you want to estimate distance of objects with your simple webcam, then this algorithm(*Triangle similarity*) would be helpful for you to find Distance *from object to camera*, I have provide to two examples, one is simple **face detection and distance Estimation**, other is **Yolo4 object detection and distance Estimation**

Here in this readme file you will get short description, if need more details, then you can watch video tutorial on YouTube as well.

## Distance & Speed Estimation Demo

https://user-images.githubusercontent.com/66181793/122644855-bb8ac000-d130-11eb-85c3-c7ff4bd6474c.mp4

### Video Tutorials

[**Distance Estimation Youtube Tutorail**](https://youtu.be/zzJfAw3ASzY) 

[**Distance & Speed Estimation Youtube Tutorial**](https://youtu.be/DIxcLghsQ4Q) 

[**YoloV4 Object Detection & Distance Estimation**](https://youtu.be/FcRCwTgYXJw) 
[*Project GitHub Repository*](https://github.com/Asadullah-Dal17/Yolov4-Detector-and-Distance-Estimator)

## YoloV4 Distance Estimation

https://user-images.githubusercontent.com/66181793/124917186-f5066b00-e00c-11eb-93cf-24d84e9c2e7a.mp4

## Distance Estimation on Raspberry Pi 🍓 

https://user-images.githubusercontent.com/66181793/138200943-74d28b4d-bd0e-49fd-8836-4a01b35118eb.mp4

✔️ here is source code and details for Instllation of Opencv-python on 🍓 Pi 😃 [Distance Estimation on Raspberry pi 🍓](https://github.com/Asadullah-Dal17/Distance_measurement_using_single_camera/tree/main/Raspberry_pi) 

:heavy_check_mark: I have included [**Speed Estimation**](https://github.com/Asadullah-Dal17/Distance_measurement_using_single_camera/tree/main/Speed) code is well check that out.

:heavy_check_mark: You can find the implementation of  [**Distance estimation of multiple objects using Yolo V4**](https://github.com/Asadullah-Dal17/Yolov4-Detector-and-Distance-Estimator) Object Detector Opencv-python

## Clone this Repo:

git clone https://github.com/Asadullah-Dal17/Distance_measurement_using_single_camera

## install Opencv-python

- Windows

  pip install opencv-python

- _install Opencv-python on Linux or Mac_

  pip3 install opencv-python

## Run the code

- windows: :point_down:

  python distance.py

  ------ OR ---------

  python Updated_distance.py

- linux or Mac :point_down:

  python3 distance.py

  ------ OR ---------

  python3 Updated_distance.py

### :bulb:_Focal Length Finder Function Description_ :bulb:

```python
# focal length finder function
def focal_length(measured_distance, real_width, width_in_rf_image):

    focal_length_value = (width_in_rf_image * measured_distance) / real_width
    #return focal length.
    return focal_length_value

```

The Focal Length finder Function Tacks Three Arguments:

`measured_distance` It is distance which we have measured while capturing reference image:straight*ruler:. \*\*\_From object to Camera*\*\* which is `Known_distance = 72.2 #centimeter`

`real_width` Its measure with width of object in real world, here i measure the width of face in real world which was `Known_width =14.3 #centimeter`

`width_in_rf_image` it width of object in the image/frame it will be in **pixels**

### :bulb:_Distance Finder Function Description_ :bulb:

```python
# distance estimation function

def distance_finder(focal_length, real_face_width, face_width_in_frame):

    distance = (real_face_width * focal_length)/face_width_in_frame
    return distance

```

This Funciton Taks Three Argument,

` Focal_Length` it is focal length, out of **FocalLength** finder function.

`real_face_width` Its measure width of object in real world, here i measure the width of face in real world which was `Known_width =14.3 #centimeter`

`face_width_in_frame` width of face in the frame, unit will pixels here.

I have also create <a href ="https://github.com/Asadullah-Dal17/Face-Following-Robot-using-Distance-Estimation"> <strong>Face Following Robot </strong> </a> which use distance Estimation, if you are interested you can Watch my<a href ="https://youtu.be/5FSOZe96kNg"> <strong>Youtube Video</strong> </a> 
You can create Face Following Robot with Raspberry that would be easy then, using Arduino Stuff, Raspberry 🍓 Pi will make it system on Robot 🤖

if You found this Helpful, please star :star: it.

You can Watch my Video Tutorial on Computer Vision Topics, just check out my YouTube Channel <a href="https://www.youtube.com/c/aiphile">  AiPhile Youtube </a>

If You have any Question or need help in CV Project, Feel free to DM on Instagram  <a href="https://www.instagram.com/aiphile17/">  Instagram </a>

## 💚🖤 Join me on Social Media 🖤💚 

<h4><a href="https://www.youtube.com/c/aiphile"> YouTube  AiPhile Youtube </a> 
 <a href="https://github.com/Asadullah-Dal17">  GitHub   GitHub </a> 
  <a href="https://medium.com/@asadullah92c">  Medium   Medium </a> 
  <a href="https://www.instagram.com/aiphile17/">   Instagram Instagram </a> </h4>

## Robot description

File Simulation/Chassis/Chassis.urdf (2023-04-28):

<?xml version="1.0" ?>
<robot name="Chassis">

<material name="silver">
  <color rgba="0.700 0.700 0.700 1.000"/>
</material>

<link name="base_link">
  <inertial>
    <origin rpy="0 0 0" xyz="1.4550500809873055e-16 0.027954839106960696 0.055"/>
    <mass value="1.0601030399999982"/>
    <inertia ixx="0.010002992865113192" ixy="4.343543488406843e-17" ixz="-4.213234205963093e-18" iyy="0.008958128284159964" iyz="3.469446951953614e-18" izz="0.01675623212271315"/>
  </inertial>
  <visual>
    <origin rpy="0 0 0" xyz="0 0 0"/>
    <geometry>
      <mesh filename="meshes/base_link.stl" scale="0.001 0.001 0.001"/>
    </geometry>
    <material name="silver"/>
    <material/>
  </visual>
  <collision>
    <origin rpy="0 0 0" xyz="0 0 0"/>
    <geometry>
      <mesh filename="meshes/base_link.stl" scale="0.001 0.001 0.001"/>
    </geometry>
  </collision>
</link>

<link name="Left_Box1">
  <inertial>
    <origin rpy="0 0 0" xyz="-0.050357220281276066 0.12100000000000122 -0.036025170819706444"/>
    <mass value="0.31751892882128063"/>
    <inertia ixx="0.0023874473680895727" ixy="2.1457288858745378e-17" ixz="-3.9675560542301244e-07" iyy="0.0006615657333269402" iyz="8.474060061821063e-18" izz="0.002463689697064902"/>
  </inertial>
  <visual>
    <origin rpy="0 0 0" xyz="0.15 0.121 -0.091"/>
    <geometry>
      <mesh filename="meshes/Left_Box1.stl" scale="0.001 0.001 0.001"/>
    </geometry>
    <material name="silver"/>
    <material/>
  </visual>
  <collision>
    <origin rpy="0 0 0" xyz="0.15 0.121 -0.091"/>
    <geometry>
      <mesh filename="meshes/Left_Box1.stl" scale="0.001 0.001 0.001"/>
    </geometry>
  </collision>
</link>

<link name="Right_Box1">
  <inertial>
    <origin rpy="0 0 0" xyz="0.050357220281276094 0.12099999999999886 -0.036025170819706506"/>
    <mass value="0.3175189288212805"/>
    <inertia ixx="0.0023874473680895705" ixy="1.4331822001797948e-17" ixz="3.967556054221451e-07" iyy="0.0006615657333269385" iyz="-1.1005335726774014e-17" izz="0.002463689697064902"/>
  </inertial>
  <visual>
    <origin rpy="0 0 0" xyz="-0.15 0.121 -0.091"/>
    <geometry>
      <mesh filename="meshes/Right_Box1.stl" scale="0.001 0.001 0.001"/>
    </geometry>
    <material name="silver"/>
    <material/>
  </visual>
  <collision>
    <origin rpy="0 0 0" xyz="-0.15 0.121 -0.091"/>
    <geometry>
      <mesh filename="meshes/Right_Box1.stl" scale="0.001 0.001 0.001"/>
    </geometry>
  </collision>
</link>

<joint name="Slider14" type="prismatic">
  <origin rpy="0 0 0" xyz="-0.15 -0.121 0.091"/>
  <parent link="base_link"/>
  <child link="Left_Box1"/>
  <axis xyz="1.0 0.0 0.0"/>
  <limit effort="100" lower="0.01" upper="0.09" velocity="100"/>
</joint>
<transmission name="Slider14_tran">
  <type>transmission_interface/SimpleTransmission</type>
  <joint name="Slider14">
    <hardwareInterface>PositionJointInterface</hardwareInterface>
  </joint>
  <actuator name="Slider14_actr">
    <hardwareInterface>PositionJointInterface</hardwareInterface>
    <mechanicalReduction>1</mechanicalReduction>
  </actuator>
</transmission>

<joint name="Slider15" type="prismatic">
  <origin rpy="0 0 0" xyz="0.15 -0.121 0.091"/>
  <parent link="base_link"/>
  <child link="Right_Box1"/>
  <axis xyz="1.0 0.0 0.0"/>
  <limit effort="100" lower="-0.09" upper="-0.01" velocity="100"/>
</joint>
<transmission name="Slider15_tran">
  <type>transmission_interface/SimpleTransmission</type>
  <joint name="Slider15">
    <hardwareInterface>PositionJointInterface</hardwareInterface>
  </joint>
  <actuator name="Slider15_actr">
    <hardwareInterface>PositionJointInterface</hardwareInterface>
    <mechanicalReduction>1</mechanicalReduction>
  </actuator>
</transmission>

</robot>

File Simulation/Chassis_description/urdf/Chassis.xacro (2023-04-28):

<?xml version="1.0" ?>
<robot name="Chassis" xmlns:xacro="http://www.ros.org/wiki/xacro">

<xacro:include filename="$(find Chassis_description)/urdf/materials.xacro" />
<xacro:include filename="$(find Chassis_description)/urdf/Chassis.trans" />
<xacro:include filename="$(find Chassis_description)/urdf/Chassis.gazebo" />
<link name="base_link">
  <inertial>
    <origin rpy="0 0 0" xyz="1.4550500809873055e-16 0.027954839106960696 0.055"/>
    <mass value="1.0601030399999982"/>
    <inertia ixx="0.010003" ixy="0.0" ixz="-0.0" iyy="0.008958" iyz="0.0" izz="0.016756"/>
  </inertial>
  <visual>
    <origin rpy="0 0 0" xyz="0 0 0"/>
    <geometry>
      <mesh filename="package://Chassis_description/meshes/base_link.stl" scale="0.001 0.001 0.001"/>
    </geometry>
    <material name="silver"/>
  </visual>
  <collision>
    <origin rpy="0 0 0" xyz="0 0 0"/>
    <geometry>
      <mesh filename="package://Chassis_description/meshes/base_link.stl" scale="0.001 0.001 0.001"/>
    </geometry>
  </collision>
</link>

<link name="Left_Box_1">
  <inertial>
    <origin rpy="0 0 0" xyz="-0.050357220281276066 0.12100000000000122 -0.036025170819706444"/>
    <mass value="0.31751892882128063"/>
    <inertia ixx="0.002387" ixy="0.0" ixz="-0.0" iyy="0.000662" iyz="0.0" izz="0.002464"/>
  </inertial>
  <visual>
    <origin rpy="0 0 0" xyz="0.15 0.121 -0.091"/>
    <geometry>
      <mesh filename="package://Chassis_description/meshes/Left_Box_1.stl" scale="0.001 0.001 0.001"/>
    </geometry>
    <material name="silver"/>
  </visual>
  <collision>
    <origin rpy="0 0 0" xyz="0.15 0.121 -0.091"/>
    <geometry>
      <mesh filename="package://Chassis_description/meshes/Left_Box_1.stl" scale="0.001 0.001 0.001"/>
    </geometry>
  </collision>
</link>

<link name="Right_Box_1">
  <inertial>
    <origin rpy="0 0 0" xyz="0.050357220281276094 0.12099999999999886 -0.036025170819706506"/>
    <mass value="0.3175189288212805"/>
    <inertia ixx="0.002387" ixy="0.0" ixz="0.0" iyy="0.000662" iyz="-0.0" izz="0.002464"/>
  </inertial>
  <visual>
    <origin rpy="0 0 0" xyz="-0.15 0.121 -0.091"/>
    <geometry>
      <mesh filename="package://Chassis_description/meshes/Right_Box_1.stl" scale="0.001 0.001 0.001"/>
    </geometry>
    <material name="silver"/>
  </visual>
  <collision>
    <origin rpy="0 0 0" xyz="-0.15 0.121 -0.091"/>
    <geometry>
      <mesh filename="package://Chassis_description/meshes/Right_Box_1.stl" scale="0.001 0.001 0.001"/>
    </geometry>
  </collision>
</link>

<joint name="Slider14" type="prismatic">
  <origin rpy="0 0 0" xyz="-0.15 -0.121 0.091"/>
  <parent link="base_link"/>
  <child link="Left_Box_1"/>
  <axis xyz="1.0 0.0 0.0"/>
  <limit effort="100" lower="0.01" upper="0.09" velocity="100"/>
</joint>

<joint name="Slider15" type="prismatic">
  <origin rpy="0 0 0" xyz="0.15 -0.121 0.091"/>
  <parent link="base_link"/>
  <child link="Right_Box_1"/>
  <axis xyz="1.0 0.0 0.0"/>
  <limit effort="100" lower="-0.09" upper="-0.01" velocity="100"/>
</joint>

</robot>

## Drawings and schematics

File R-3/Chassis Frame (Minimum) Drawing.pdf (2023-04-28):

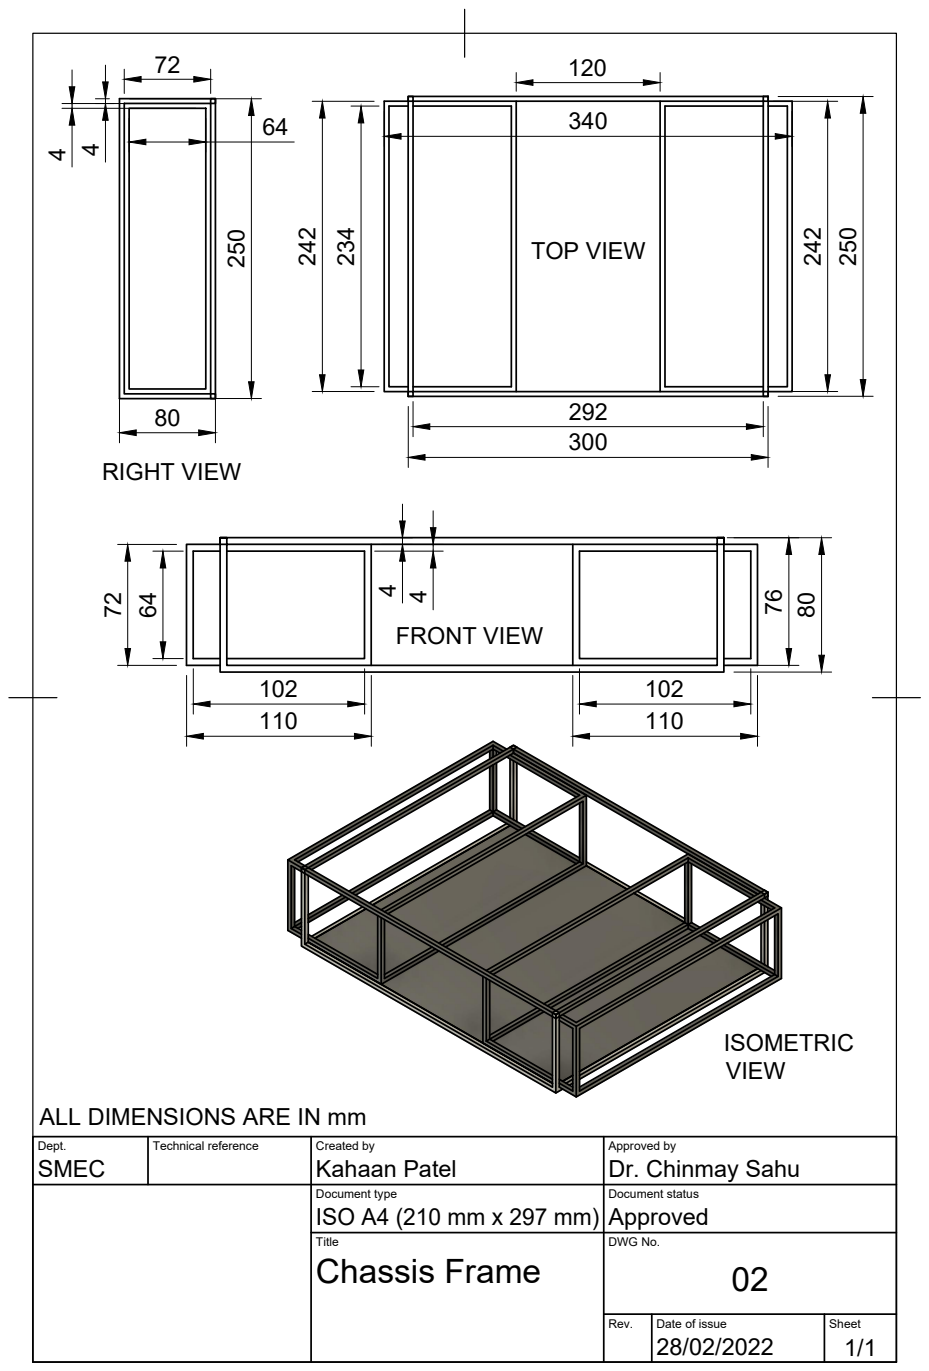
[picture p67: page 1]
RIGHT VIEW; FRONT VIEW

TOP VIEW

ALL DIMENSIONS ARE IN mm

Dept. SMEC | Technical reference | Created by Kahaan Patel | Approved by Dr. Chinmay Sahu

Document type ISO A4 (210 mm x 297 mm) | Document status Approved

Title Chassis Frame | DWG No. 02

Rev. | Date of issue 28/02/2022 | Sheet 1/1

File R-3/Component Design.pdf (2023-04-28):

A
A-A (1.5:1) 3.56 3.35

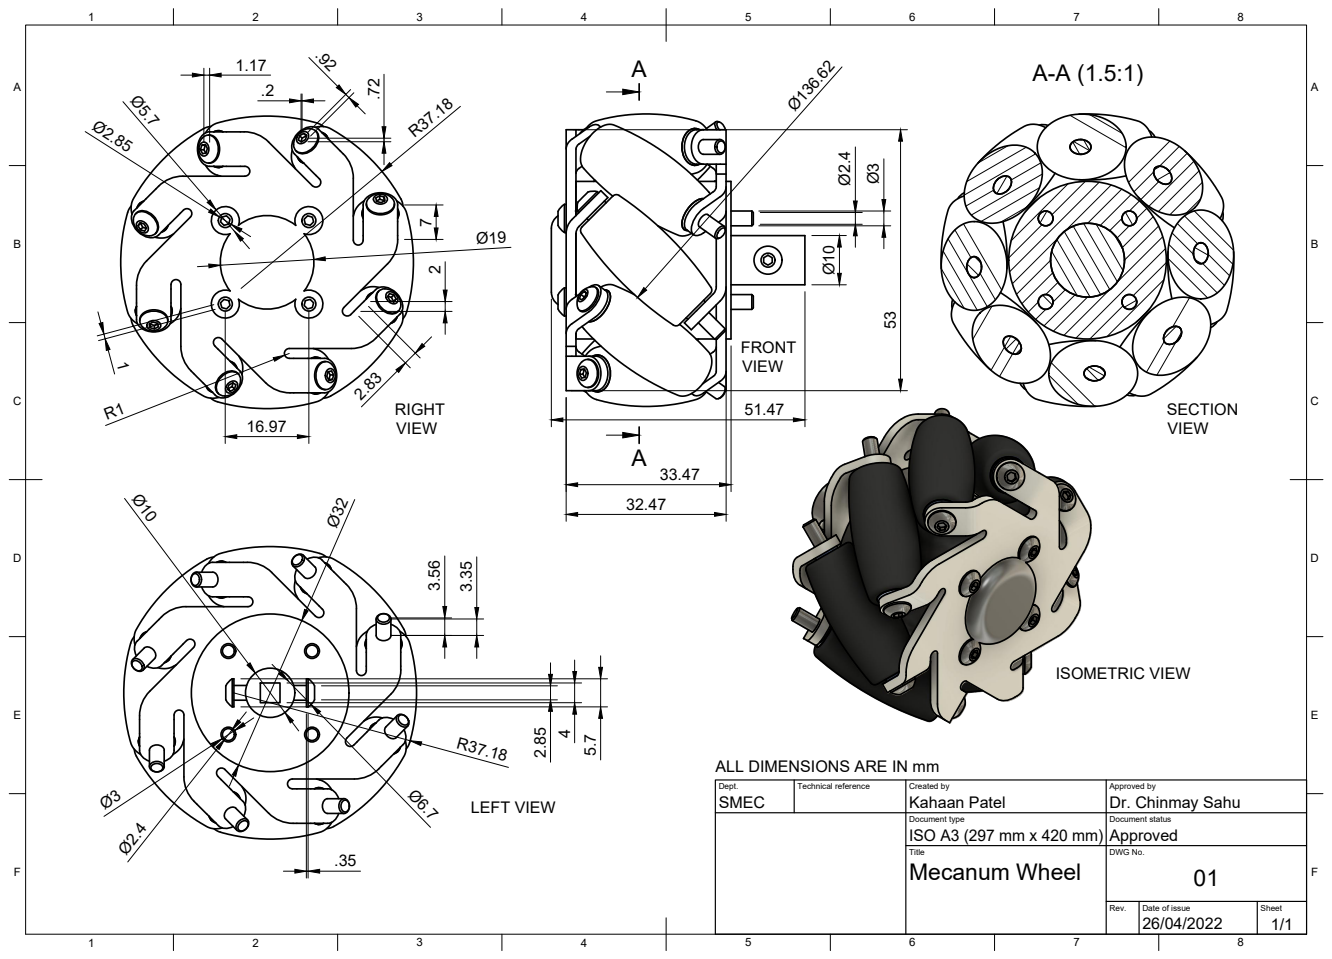
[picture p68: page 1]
Dept.; Technical reference; Created by; Approved by; Document type; Document status; Title; DWG No.; Rev.; Date of issue; Sheet; ISO A3 (297 mm x 420 mm); Approved; Mecanum Wheel; SMEC; Kahaan Patel; Dr. Chinmay Sahu; RIGHT; VIEW; LEFT VIEW; FRONT VIEW; SECTION VIEW; ISOMETRIC VIEW

ALL DIMENSIONS ARE IN mm

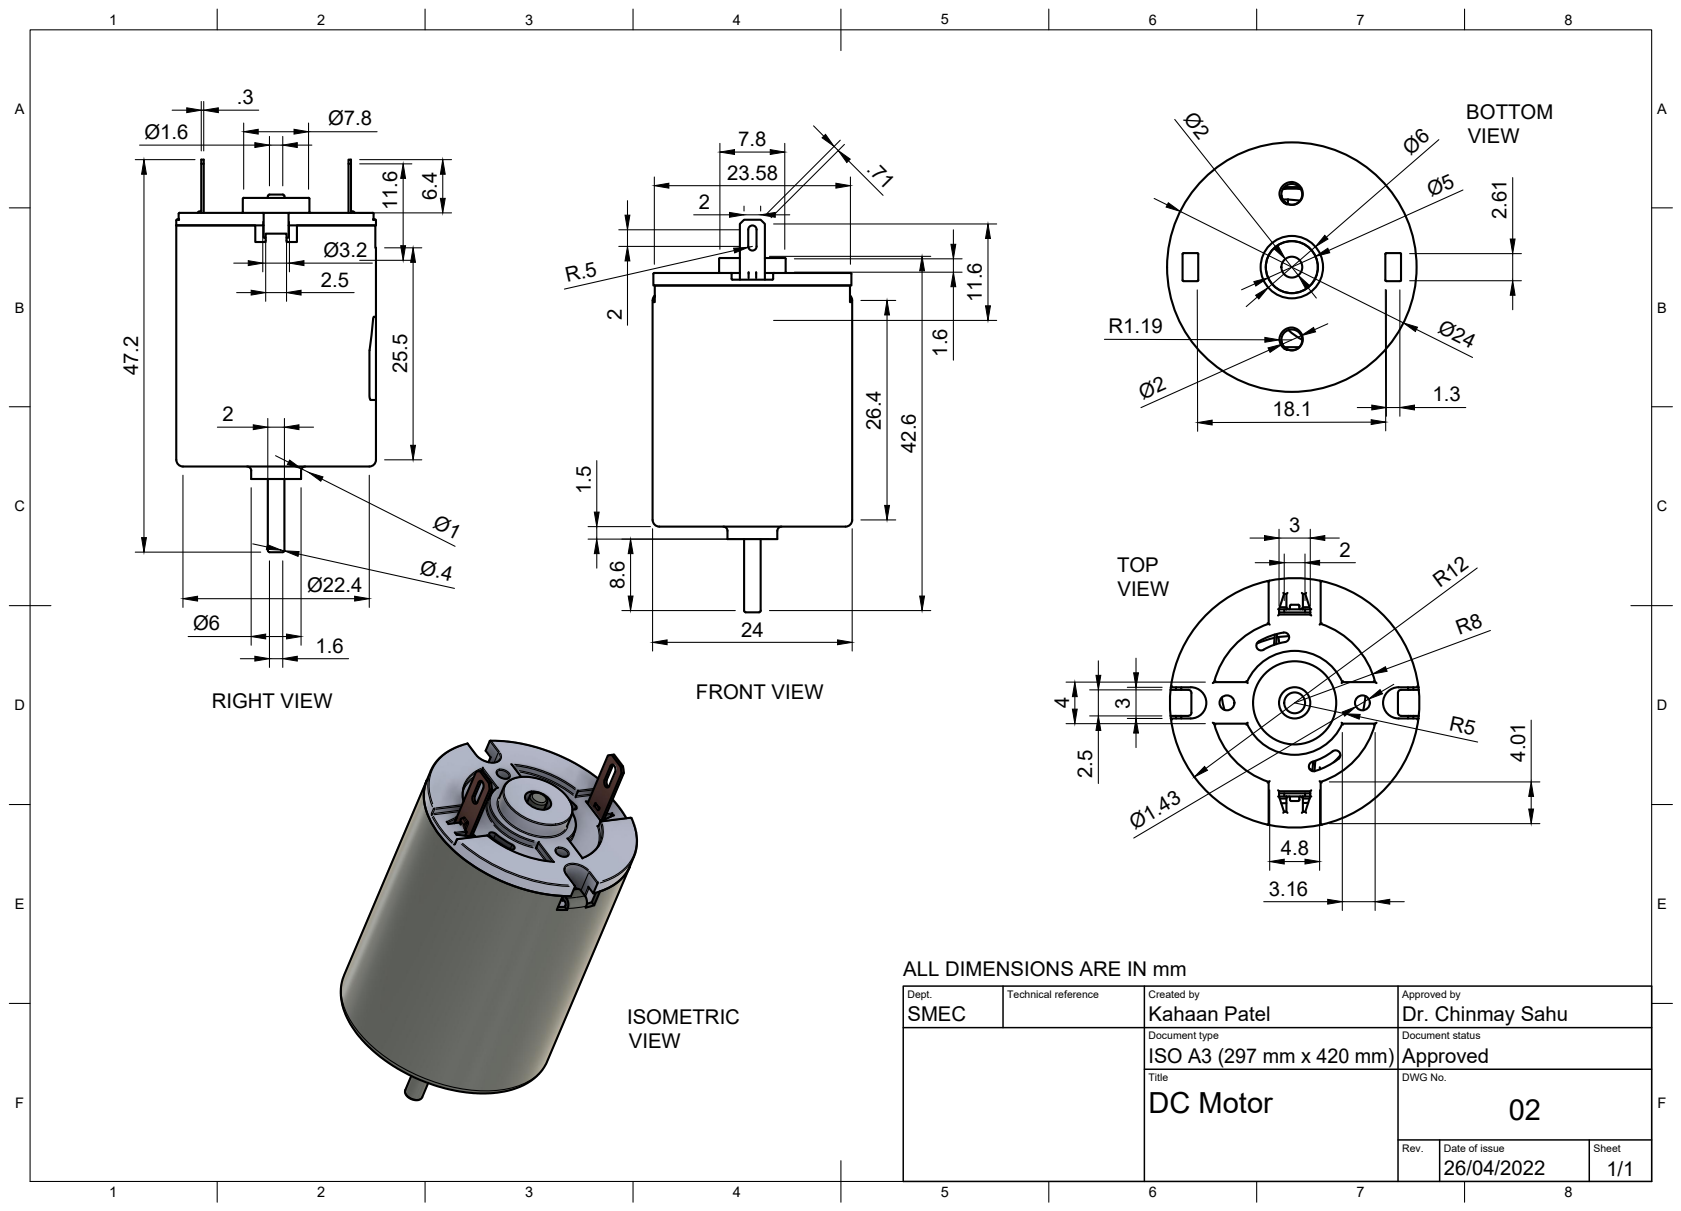
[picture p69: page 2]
Dept.; Technical reference; Created by; Approved by; Document type; Document status; Title; DWG No.; ISO A3 (297 mm x 420 mm); Approved; DC Motor; SMEC; Kahaan Patel; Dr. Chinmay Sahu; RIGHT VIEW; FRONT VIEW; BOTTOM VIEW; TOP VIEW; ISOMETRIC VIEW

ALL DIMENSIONS ARE IN mm

.26 ⁶.41

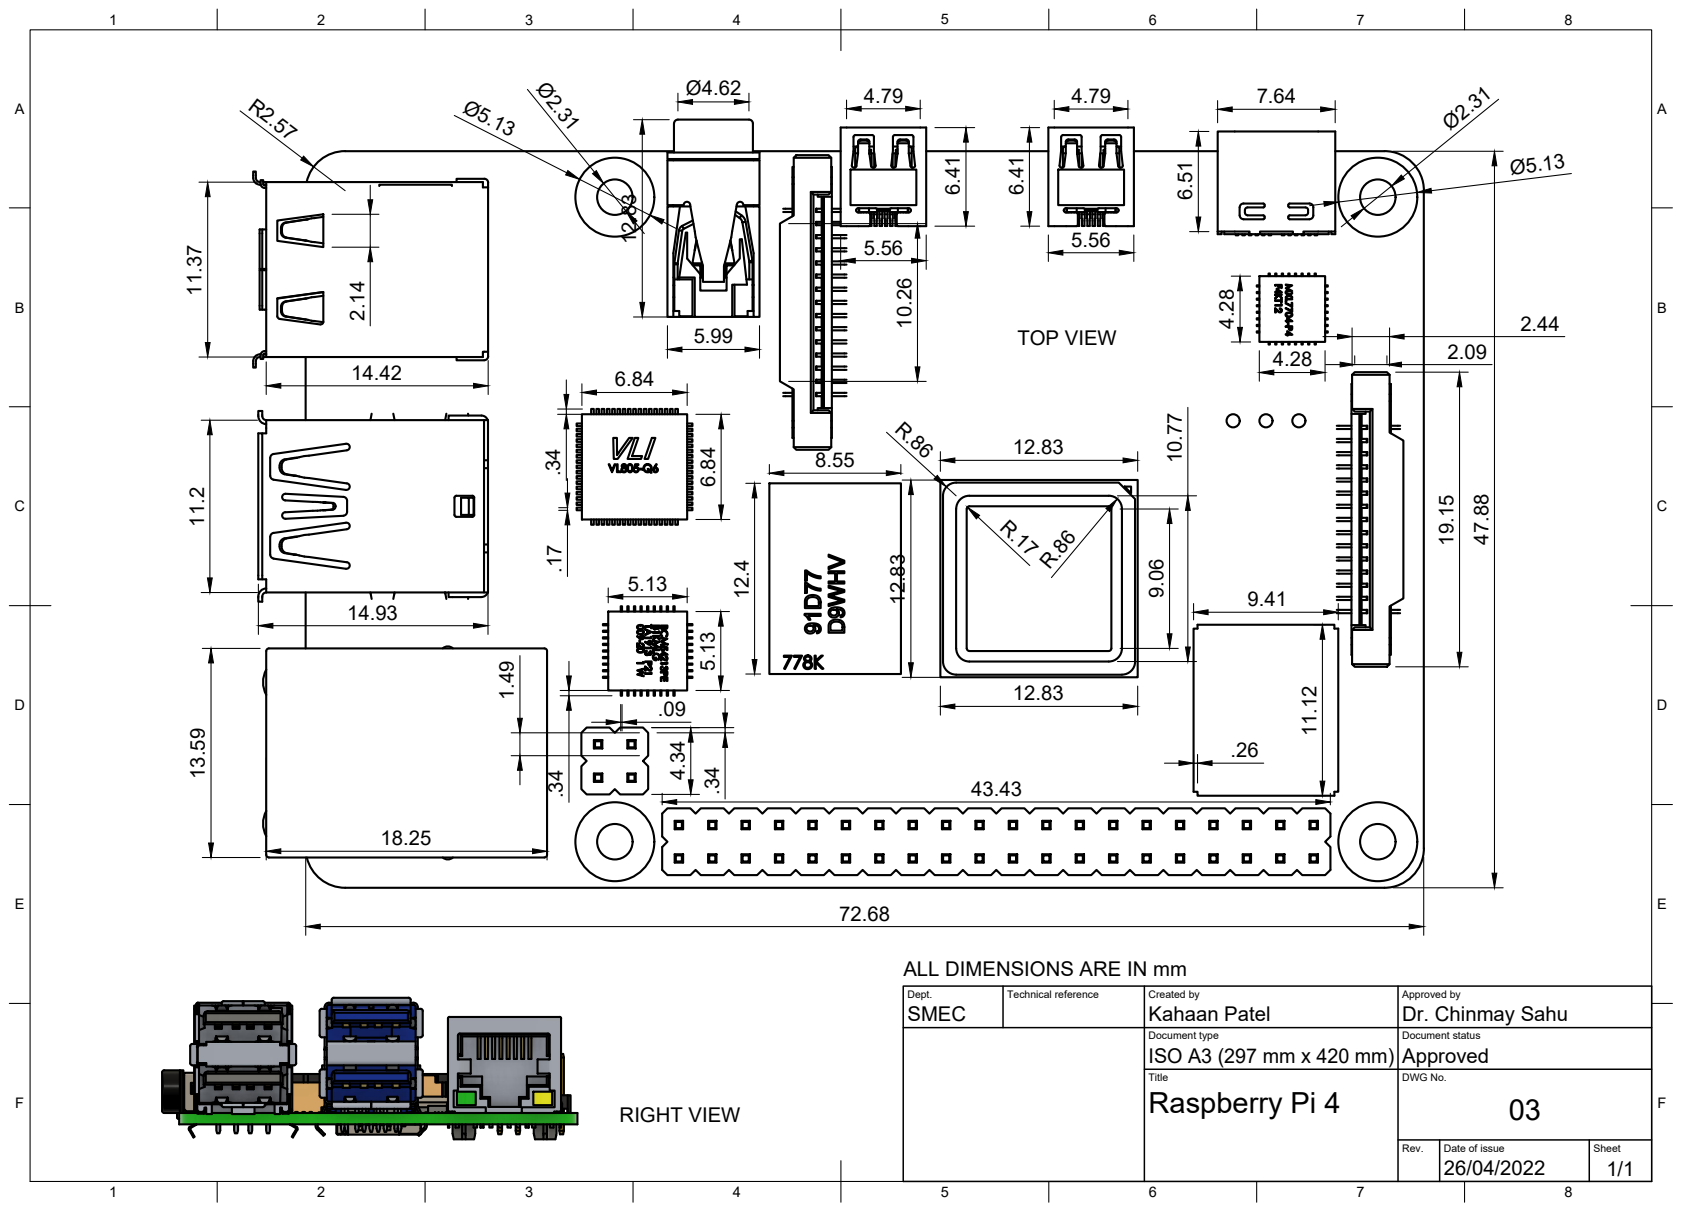
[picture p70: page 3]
Dept.; Technical reference; Created by; Approved by; Document type; Document status; Title; DWG No.; ISO A3 (297 mm x 420 mm); Approved; Raspberry Pi 4; SMEC; Kahaan Patel; Dr. Chinmay Sahu ⁴⁷.88; TOP VIEW; RIGHT VIEW

ALL DIMENSIONS ARE IN mm

11.6 4.8 23.2

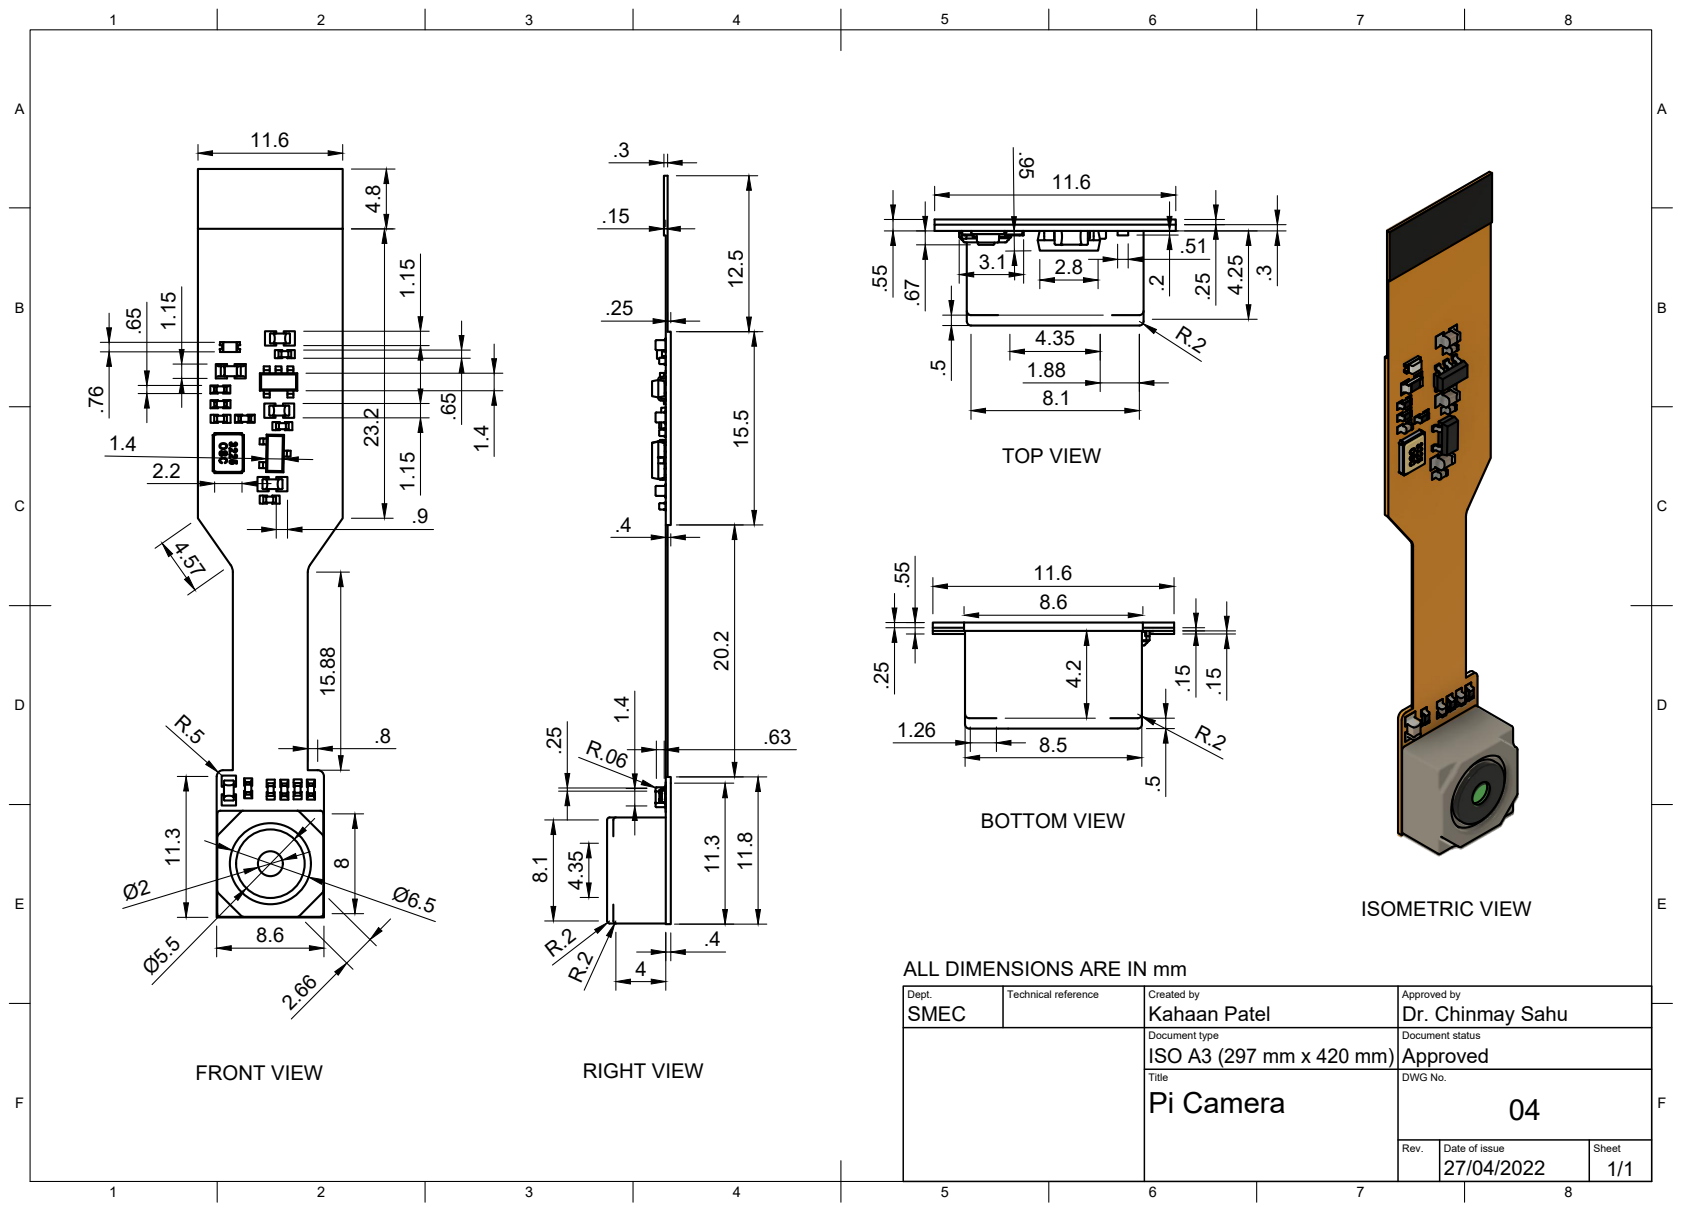
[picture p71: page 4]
Dept.; Technical reference; Created by; Approved by; Document type; Document status; Title; DWG No.; ISO A3 (297 mm x 420 mm); Approved; Pi Camera; SMEC; Kahaan Patel; Dr. Chinmay Sahu; FRONT VIEW; RIGHT VIEW; TOP VIEW; BOTTOM VIEW; ISOMETRIC VIEW

ALL DIMENSIONS ARE IN mm

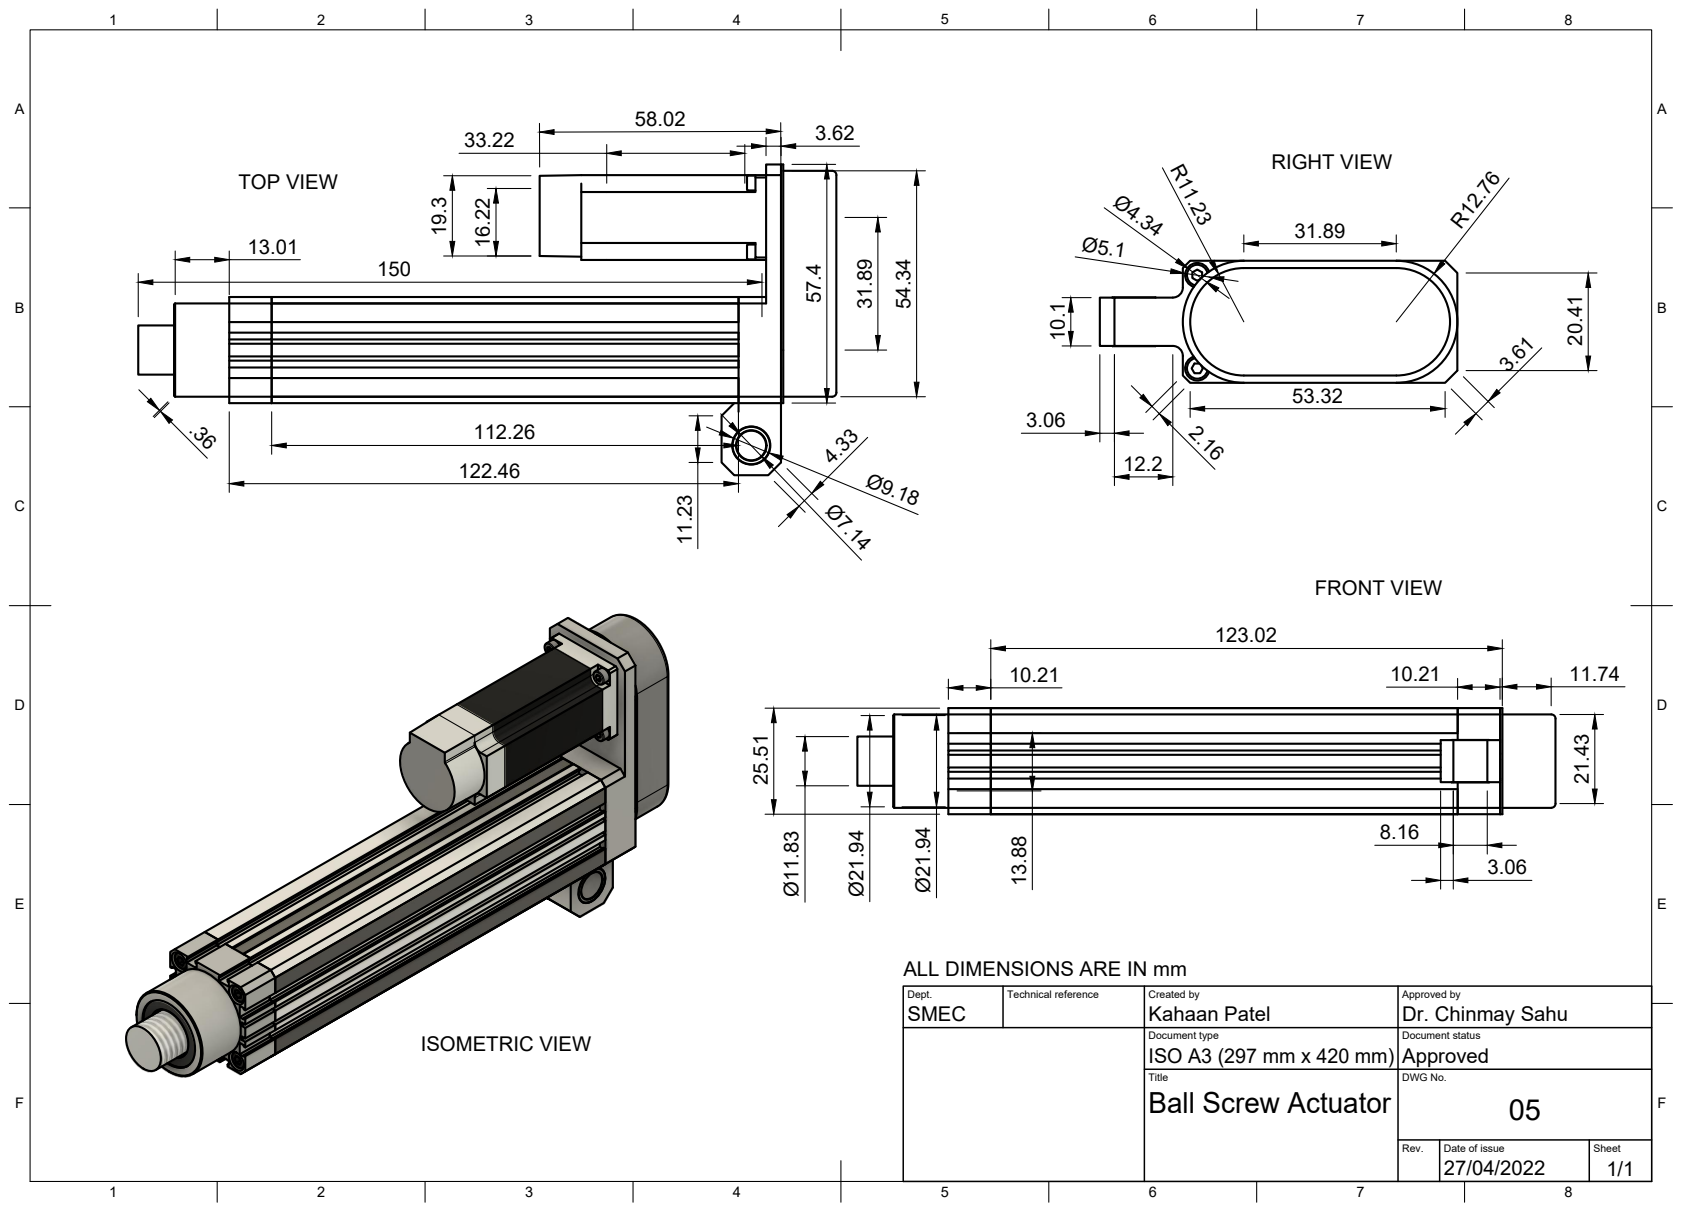
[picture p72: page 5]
Dept.; Technical reference; Created by; Approved by; Document type; Document status; Title; DWG No.; ISO A3 (297 mm x 420 mm); Approved; Ball Screw Actuator; SMEC; Kahaan Patel; Dr. Chinmay Sahu; 57.4 Ø¹¹.83; Ø²¹.94; Ø²¹.94 25.51; TOP VIEW; RIGHT VIEW; FRONT VIEW; ISOMETRIC VIEW

ALL DIMENSIONS ARE IN mm

A

A-A

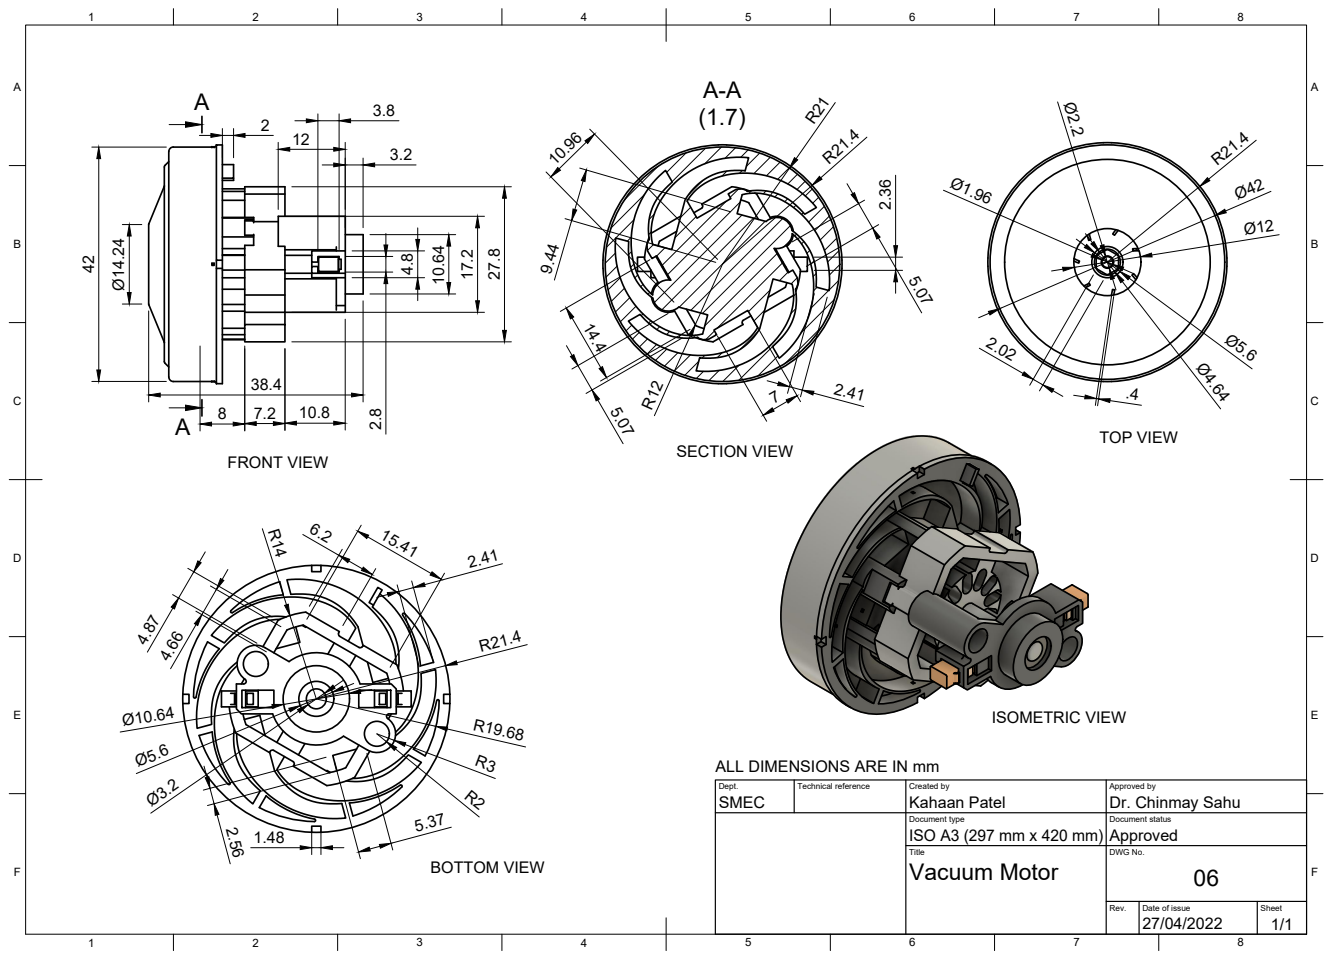
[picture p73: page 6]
Dept.; Technical reference; Created by; Approved by; Document type; Document status; Title; DWG No.; ISO A3 (297 mm x 420 mm); Approved; Vacuum Motor; SMEC; Kahaan Patel; Dr. Chinmay Sahu; Ø¹⁴.24; FRONT VIEW; BOTTOM VIEW; SECTION VIEW; TOP VIEW; ISOMETRIC VIEW

ALL DIMENSIONS ARE IN mm

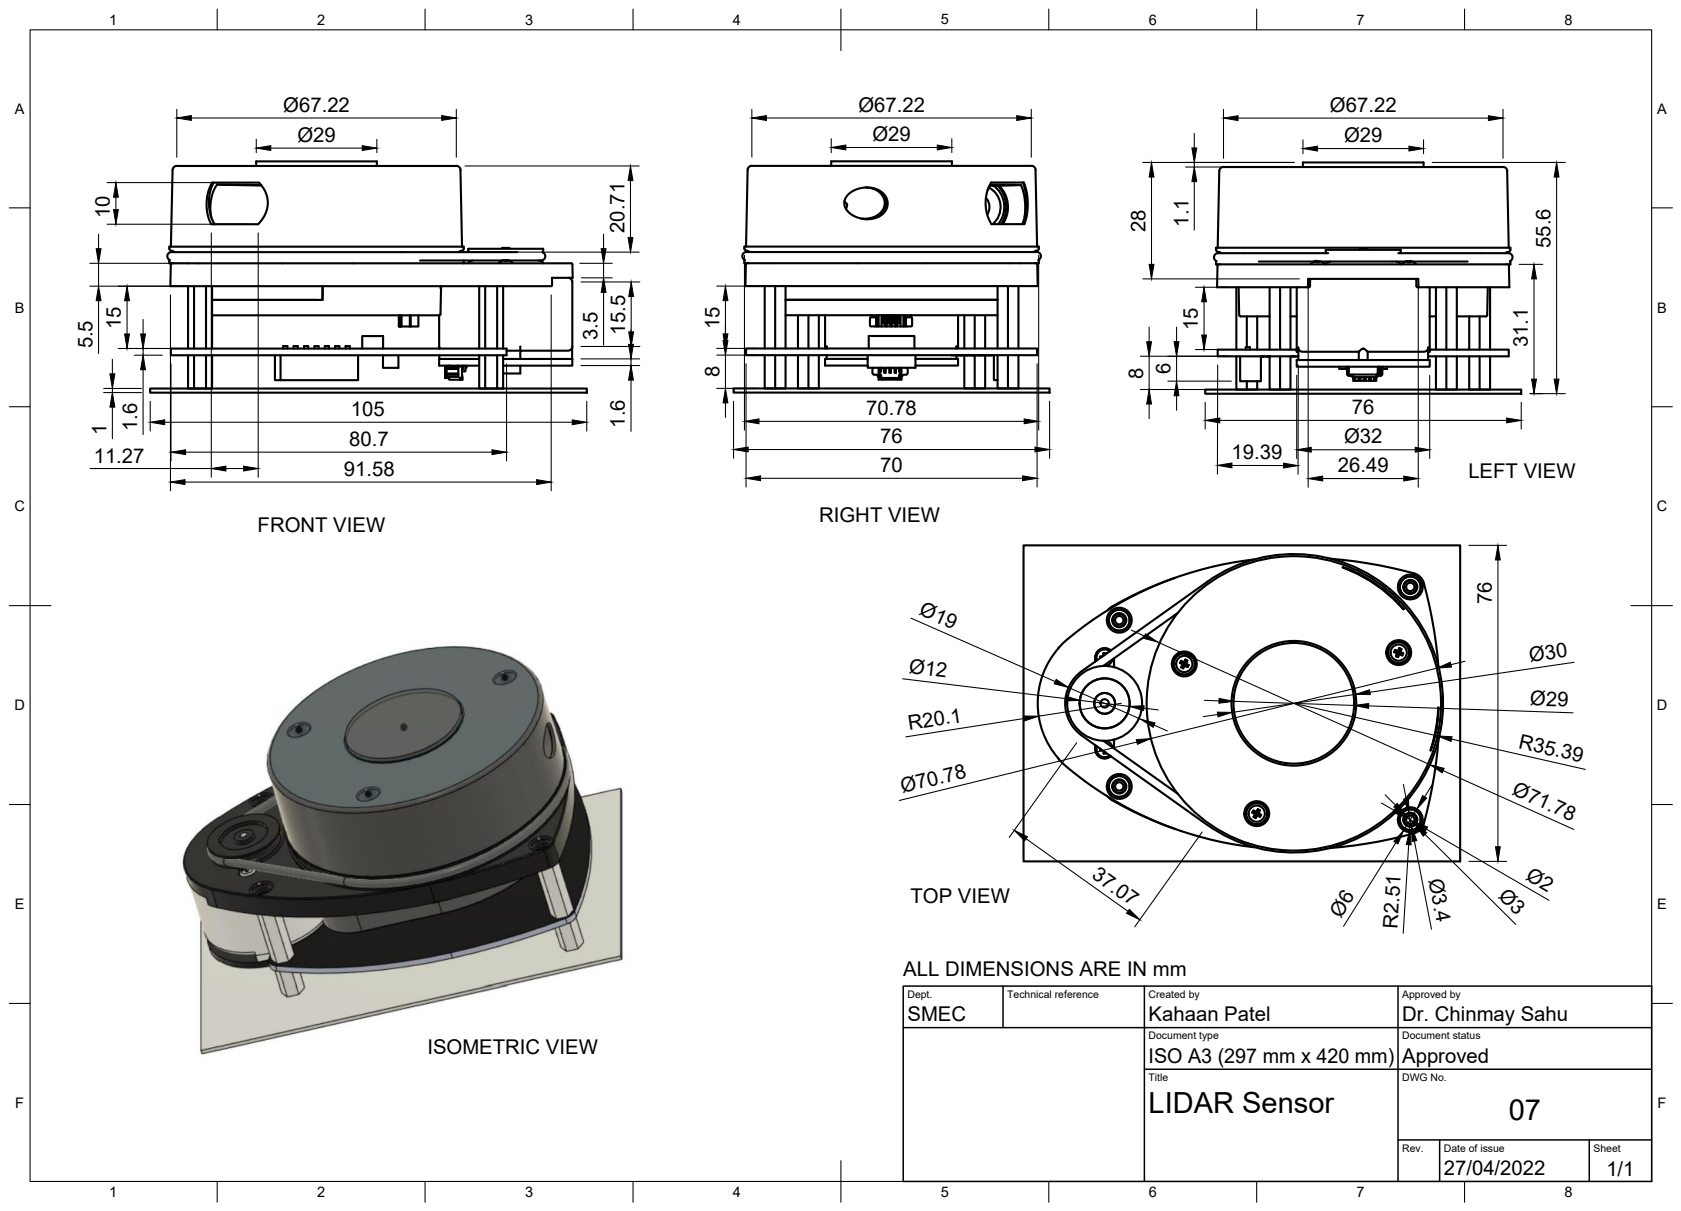
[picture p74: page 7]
Dept.; Technical reference; Created by; Approved by; Document type; Document status; Title; DWG No.; ISO A3 (297 mm x 420 mm); Approved; LIDAR Sensor; SMEC; Kahaan Patel; Dr. Chinmay Sahu; FRONT VIEW; RIGHT VIEW; LEFT VIEW; TOP VIEW; ISOMETRIC VIEW

ALL DIMENSIONS ARE IN mm

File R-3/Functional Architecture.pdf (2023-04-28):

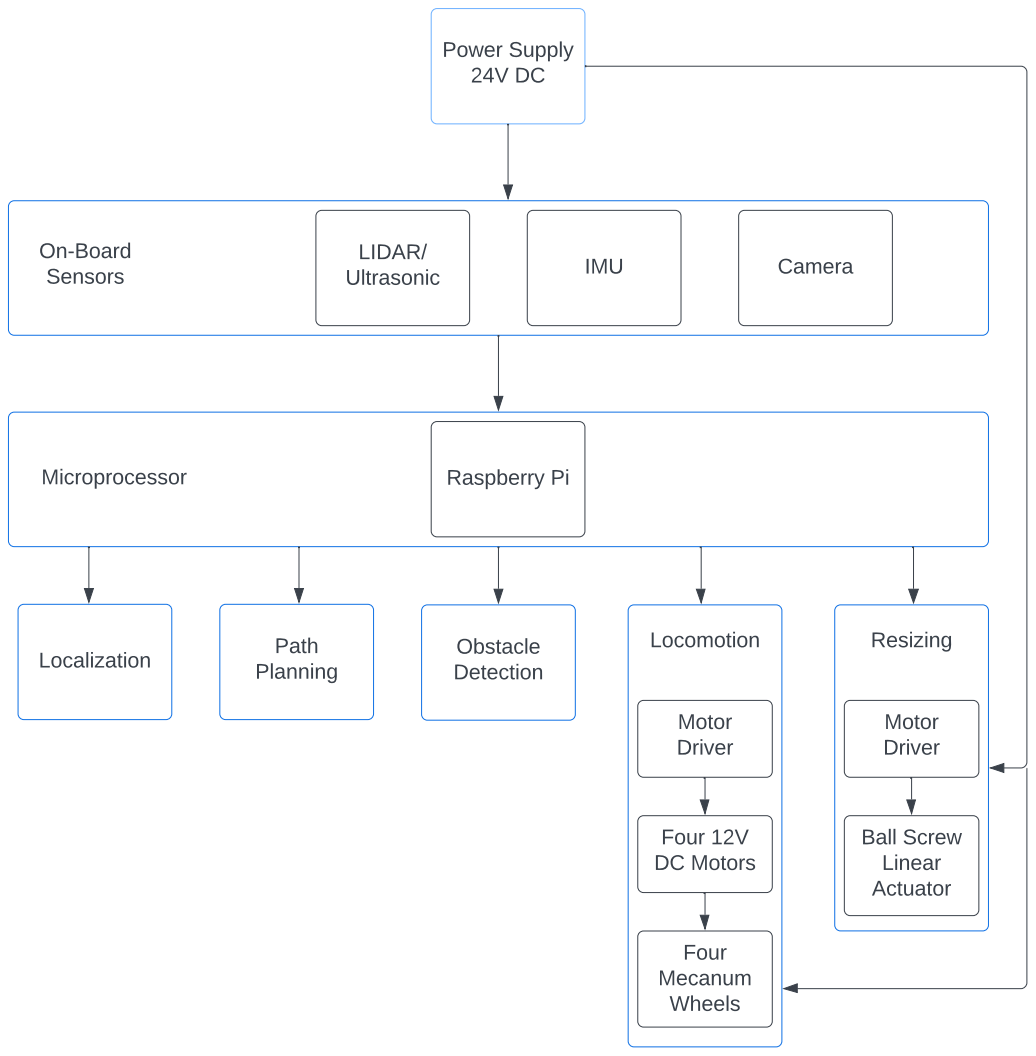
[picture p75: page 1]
Power Supply 24V DC; LIDAR/ Ultrasonic; IMU; Camera On-Board; Sensors; Microprocessor; Raspberry Pi; Localization; Path; Planning; Obstacle Detection; Locomotion; Motor Driver; Four 12V DC Motors; Resizing; Ball Screw Linear Actuator

Four Mecanum Wheels

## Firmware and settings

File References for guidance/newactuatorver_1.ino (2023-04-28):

#include <Servo.h>
#include <UltrasonicSensor.h>

UltrasonicSensor ultrasonic(11, 12);

int mm=0;
int cm=0;
Servo myservo;  
int distanc=0;
int pos = 0;  

void setup() {
  
  myservo.attach(9);
  Serial.begin(9600);
  // attaches the servo on pin 9 to the servo object

}

void loop() {
  
  distance = ultrasonic.distanceInMillimeters();
  pos= Serial.read();
  Serial.println("position to go");
  Serial.print(pos);
  if (pos > distance){
    Serial.println(distance);
   
    if (pos!=distance){
      myservo.write(180); 
       if(pos==distance){
      myservo.detach();
    }
    }
   
    Serial.println(distance);

  }

  if(pos<distance){
     if (pos!=distance){
      myservo.write(0); 
       if(pos==distance){
      myservo.detach();
    }
  }}

   if(pos==distance){
      myservo.detach();
    }

//  for (mm = 0; mm <= 11; mm += 1) { // goes from 0 degrees to 180 degrees
//    // in steps of 1 degree
//    myservo.write(180);              // tell servo to go to position in variable 'pos'
//    delay(1130);  
//    Serial.println(mm);            // waits 15ms for the servo to reach the position
//  }
// 
//  mm=0;
//  cm=cm+1;
//  Serial.println(cm);

}

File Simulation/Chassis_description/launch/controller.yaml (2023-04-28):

Chassis_controller:
  # Publish all joint states -----------------------------------
  joint_state_controller:
    type: joint_state_controller/JointStateController
    publish_rate: 50

  # Position Controllers --------------------------------------
  Slider14_position_controller:
    type: effort_controllers/JointPositionController
    joint: Slider14
    pid: {p: 100.0, i: 0.01, d: 10.0}
  Slider15_position_controller:
    type: effort_controllers/JointPositionController
    joint: Slider15
    pid: {p: 100.0, i: 0.01, d: 10.0}
